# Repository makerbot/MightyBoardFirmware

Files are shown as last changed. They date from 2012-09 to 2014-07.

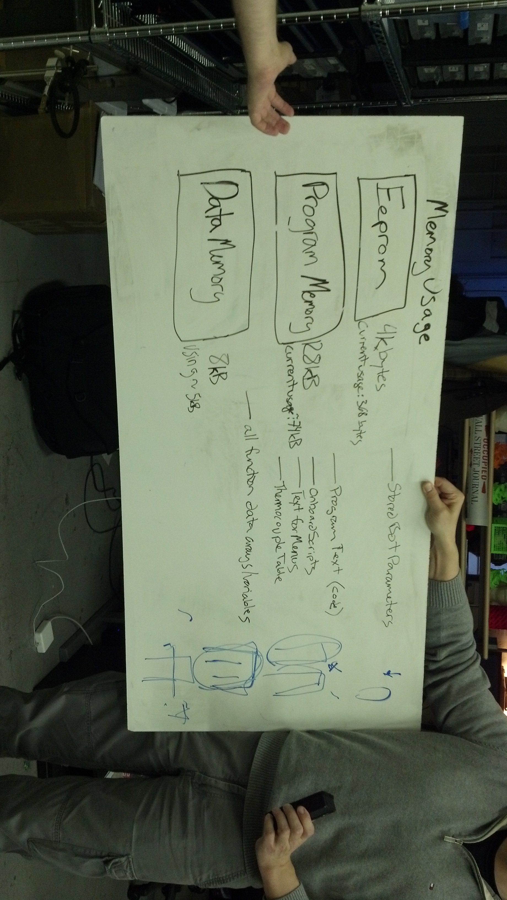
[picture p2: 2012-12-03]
docs/memory_usage.jpg

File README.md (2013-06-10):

Replicator MightyBoard Firmware
===============================

This is the firmware repository for the Replicator, Replicator Dual, Replicator 2 & 2X desktop 3D-printing machines.

If you're getting started, please begin by reading the documentation for
the firmware:
http://wiki.makerbot.com/v2-firmware

This project contains the following subdirectories:
* firmware - this is the firmware, where active development takes place.
       See http://wiki.makerbot.com/v2-firmware for details on how to
       build and install the code.
* bootloader - this contains the bootloaders for the MCUs on the Mightyboard
* dist - this directory contains tools and scripts for quickly installing
       bootloaders and board images for the MightyBoard
* tests - this directory contains tests using the s3g driver and development testing data
* docs - info about command handling and firmware details

N.B. to generate the french version of the firmware, add the LOCALE=fr env
variable before compiling

To use the tests in s3g_tests, you must initialize the s3g submodule by running
git submodule init
git submodule update

Build the latest firmware version
===

___These instructions only apply to Mac OS X for now.___

You must first install `SCons` and `avr-libc` if you don't have it :

    $ brew install scons

Then :

    $ brew tap larsimmisch/avr
    $ brew install avr-libc --env=std

If you wish to upload, you must install `avrdude` if it is not yet present :

    $ brew install avrdude

> NB : if you haven't got `brew` installed, see http://mxcl.github.io/homebrew/ .

Make sure that you have installed the command line tools from Xcode. If you run into any problem while compiling, it may mean that you need to update your developer folder :

    $ sudo xcode-select -switch /Applications/Xcode.app/Contents/Developer/

If everything is fine, you should be able to run `xcrun -find gcc` and have the following output :

    $ xcrun -find gcc
    /Applications/Xcode.app/Contents/Developer/usr/bin/gcc

And at least these packages :

    $ brew list 
    [...] avr-binutils  avrdude  avr-gcc   avr-libc  libmpc  mpfr  scons [...]

To create the documentation, you will also need `doxygen` (and `graphviz` for nice vizualisations) :

    $ brew install doxygen
    $ brew install graphviz

Then, run :

    $ ./firmware/build_and_upload.sh

You will be prompted for the Replicator type (A or B for `mighty_one` or `mighty_two`, default: `mighty_two`) and the locale to use (available : `fr` and `en`, default : `en`). The script will build the firmware from the sources in the given locale and ask to upload to the connected Replicator.

> NB : A build output log is generated in `./firmware/build_and_upload.log`

Cleaning up
===

You can clean up a previously built version with :

    $ ./firmware/cleanup.sh [-f]

The `-f` option cleans up without prompting for confirmation.

Uploading only
===

To upload a new firmware to a Replicator via USB :

    $ ./dist/MightyBoard/load_firmware_usb.sh mighty_two_v7.3.10.hex /dev/tty.usbmodem*

where `mighty_two_v7.3.10.hex` is the corresponding firmware HEX file and `/dev/tty.usbmodem*` the port to use (this is the default port for all USB connectors on a Mac).

- - -
 
Credits 
=======

  - French localization ( < 7.2 ) : guyzmo (CKAB)
  - French localization ( > 7.2 ) : tchapi (CKAB)
  - Scripts improvements, updates and fixes : tchapi (CKAB) - 2013

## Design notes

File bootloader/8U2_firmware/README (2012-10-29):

The Makerbot usbserial 8U2 firmware is based on Arduino's 8U2 usbserial firmware.  Thanks Arduino! (www.arduino.cc)
...And that firmware is based on LUFA (See the LUFA/readme.txt and LUFA/License.txt file).

The Makerbot 8U2 Source Code can be found in the src/Projects/makerbot directory

*Note, a .inf Driver file is required to use the MightyBoard with windows.  It can be found in the ReplicatorG drivers folder.

TO DOWNLOAD THE HEX FILE:
1. Connect the AVR ISP MKII compatible programmer to the 8U2 6 pin programming header
2. Ensure the Board is Powered
3. navigate to the directory containing the .hex file in the terminal
4. Execute the following avrdude command: avrdude -p at90usb82 -F -P usb -c avrispmkii -U flash:w:Makerbot-usbserial.hex -U lfuse:w:0xFF:m -U hfuse:w:0xD9:m -U efuse:w:0xF4:m -U lock:w:0x0F:m
5. If unsuccessful ("Error in USB Receive"), try again.  It sometimes takes a few tries

IF YOU NEED TO RECOMPILE THE HEX FILE:
*This is only necessary if you have made changes to the 8U2 Source Code
*This works with avr-gcc v4.3.3 on Mac osx.  It does not work with avr-gcc v4.5.3 on ubuntu. Testing with alternate gcc versions has not been done
1. Enter the makerbot project directory in the terminal
2. Run "make clean"
3. Run "make"
4. Your hex file will be generated in the currect directory

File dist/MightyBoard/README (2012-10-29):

#Uploading bootloaders + firmware

To use the firmware upload script, you must have avrdude installed on your machine.  To install, see instructions here: http://wiki.makerbot.com/v2-firmware

Note that these instructions include installing scons and avr-gcc which are tools required to build the firmware from source.  If you just want to upload firmware binaries using the scripts in this folder, you can skipp these steps and just install avrdude.

We use an avrisp mkii to upload bootloaders.  Other isp tools can be used, just edit the .sh script appropriately.  The avirisp mkii has a red line on the cable indicating pin one.  On the mighty_board one (revE), pin one is indicated with a small circle.  On Mightyboard two (revG), pin one is indicated with a longer white line next to the pin.

From the command line run:

./load_firmware.sh firmware_filename.hex usb_port

-firmware_filename.hex is the .hex binary firmware file  (default: mighty_two_v5.5.hex)
-usb_port is the port used to upload firmware over usb (default: /dev/ACM0)

1. wait for script prompt for 8U2
2. connect the avrisp mkii to the ISP pins for the 8U2, press enter
3. wait for script prompt for 1280 bootoader
4. connect the avrisp mkii to the ISP pins for the 1280, press enter
5. (occasional step) if the script asks you to switch a fuse back (y/n), choose y
6. wait for the script prompt for the 1280 firmware
7. connect the usb cable to the mightyboard usb port, remove the avisp mkii from the 1280 ISP pins, press enter

the script will report success or fail for each step.  if you have failures, the script runs in a loop and you can run it again by continuing to press enter.  if all steps are successful, hit control-C to quit

#Uploading firmware only via USB
(bootloaders must be loaded for upload over USB to work)

from the command line run:

./load_firmware_usb.sh firmware_filename.hex usb_port

-firmware_filename.hex is the .hex binary firmware file  (default: mighty_two_v5.5.hex)
-usb_port is the port used to upload firmware over usb (default: /dev/ACM0)

press enter when prompted to upload firmware.  keep in mind the following:

1. mightyboard must be connected to usb_port
2. mightyboard must be powered on
3. bootloaders must be loaded successfully prior
4. the serial port cannot be open with repG or other serial host
5. the auto reset will not work if the serial port has not been opened immediately prior with pyserial or avrdude @ 57600baud.  If this is the case, use pyserial or avrdude to open a connection to the board at 115200 (or any baud rate not 57600), then run ./load_firmware_usb.sh again and the auto reset will work.  alternatively, you can manually press the reset button on the mightyboard at the same moment as starting the script to force a reset.

if upload is successfull, press control-C to exit.  if desired, the script will run in a loop indefinitely.

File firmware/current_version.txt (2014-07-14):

7.6.1.1.0
 * PID loop values changed to handle Rep2X extruder heating issues
 * (PID loop) ErrorAccumulator max set to 512 instead of 256
7.5.5.1.0
 * Fix for change filament timeouts ending in non-resumable prints
7.5.4.1.0
 * Update to Rep1(Dual) statup script so that loading the right extruder makes sense
7.5.3.1.0
 * Fix for heat hold USB print canceling scenarios
7.5.2.1.0
 * Fix for heat hold interfering with preheat, and filament loading after a canceled build
7.5.1.1.0
 * Removal of dual filament loading for Rep2X startup script
 * Fix for Heat Hold not being handled properly
 * Fix for bot type errors causing builds to "unattach" from the UI
 * Fix for bot type errors causing builds to not return to the SD Menu
7.4.1.1.0
 * Fix for build time rollover bug, 
 * Added fix for the button array setup
 * Disable z pause when a build is canceled
7.3.13.1.0
 * fix box display bug in heat up
7.3.12.1.0
 * HBP update rate set to 500ms
7.3.11.1.0
 * fixed bug in heating up bar, updated z pause height behavior
7.3.210.1.0
 * testing version to check for memory overruns
7.3.10.1.0
 * Added feature to return the screen to the SD Card menu after an SD card build.
7.3.9.1.0
 * Fixed alignment issues in Menu_locales.hh
7.3.8.1.0
 * Fixed JIRA bug MW-946. When the printer is in the paused state and the user presses "Back to Monitor", the print resumes.
7.3.7.1.0
 * Fixed JIRA bug MW-952. Following a mid-print filament change, the "Resume Build" item is still available on the menu.
7.3.6.1.0
 * Fixed not resetting of Z Pause Height enable after a Z Pause Height condition.
 * Changed behaviour of Done! within Z Pause Height menu, it now goes to the build screen.
7.3.5.1.0
 * Fixed bug preventing user from resuming their print after a timeout in the change filament mode.
7.3.4.1.0
 * Changed behaviour of Z Pause Height behaviour, it now goes into active build menu when triggered
7.3.3.1.0
 * Added timeout to change filament mode as the motors are staying at full torque
 * Corrected issue that prevented the printer from checking for heaters not working
7.3.2.1.0
 * Fixed temperature conversion table inconsistencies
 * Added error numbers to all heater failures
 * Added new errors for heater failures that check for proper configuration byte to be read back from both channels
 * Some heater failures now cause the printer to stop printing
 * Added slower SD card fix for Rev H boards
7.3.1.1.0
 * XY motor torque is no longer turned down when in Change Filament mode allowing the print to resume from the same spot easier on Rep 2x
 * Added Z Pause Height feature, pausing the print at a specified height in mm
 * Fixed missing letters in text displayed on LCD
 * Added print time, toggle between percent complete and print time
 * Corrected some inconsistencies with temperature reading tables
7.2.1.1.0
 * removed post level print
7.1.3.1.0
 * fixed text alignment issue
7.0.0.1.0
 * french build - not going to worry about the fact the the french makerbots have a slightly different versioning scheme
7.1.3.1.0
 * fixed text alignment issue
7.1.2.1.0
 * fixed "retry" in level plate
 * fixed the LevelPlate TestPrint brokeness
7.1.1.1.0
 * beta version of 7.1 - the LevelPlate TestPrint is broken in this build
7.0.8.1.0
 * fixes issue in ReplicatorG where the bot starts before the extruder reaches temperature
7.0.7.1.0
 * fixes to preheat behavior and sleep
7.0.6.1.0
 * sd card menu reversed
7.0.5.1.0
 * heat behavior fixes, 2X support adds
7.0.3.1.0
 * version number bump since we haven't release in a while 
7.0.1.1.0
 * x3g version number bump
6.2.30.1.0
 * x3g firmware, active build menu re-org
6.2.29.1.0
 * tall boy firmware for aljosa
6.2.28.1.0
 * enable reversed for Ben and Harry 
6.2.27.1.0
 * edit eeprom map to fix downgrade breakage
6.2.26.1.0
 * minor version number bumped to 2 to accomodate a bug fix on 6.0
6.1.26.1.0
 * internal release only minor updates required for future
6.1.25.1.0
 * internal release middle updates
6.1.24.1.0
 * internal release with stream version numbers
6.1.23.1.0
 * internal release with stream version numbers
6.1.22
 * internal release with jetty acceleration + eeprom changes
6.0.21
 * this is a merge of the jetty acceleration (more better!)
6.0.20
 * same as 5.05.20 with major version number bumped to 6.0
5.05.20
 * internal release - release candidate September 16 2012
5.05.19
 * internal release September 13 2012
6.00.18
 * internal release September 12 2012
5.05.16
 * internal release August 31, interface minor re-org
5.05.15
 * internal release August 23, minor menu fixes
5.05.14
 * internal release August 23, small bug fixes
5.05.13
 * internal release August 21, interface final beta
5.05.12
 * internal release August 17, 2012 with nozzle offsets updated
5.05.09
 * internal release August 13, 2012 no z-clipping version for engineering.
5.06.08
 * internal release Sept 12, 2102
5.05.07
 * internal release July 31, 2012 interface feature updates
5.05.06
 * internal release July 26, 2012 build for mighty_one
5.05.04
 * internal release July 18, 2012 debug stalls using atomic blocks on move commands
5.05.03
 * internal release July 18, 2012, pause menu updates
5.05.02
 * internal release July 12, 2012, replicactor 2 steps per mm
5.05.01
 * internal release July 12, 2012
5.05
 * release for acceleration
5.04
 * fixes for acceleration
5.03
 * bug fix release / acceleration beta
5.02
 * added Tolerance offset for nozzles

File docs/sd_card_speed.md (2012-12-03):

##SD Card Speed Requirements

Note: We should measure both the command processing time and the sd card block read time with the logic analyzer to have a more accurate estimate.  

SD Card Block: 512 Bytes (we read sd card data in blocks at a time)

Command Buffer: 512 Bytes

Extended Move Command: 31 bytes

Moves per Block : 16 moves (512/31)

Approximate time for command processing : 2ms (we should measure this again - this estimate is from memory)

Time to Process 1 block of commands : 32ms (16 *2ms -- subject to check above)

Note: Timing was measured at unknown start/ end points - timing may not be multiplicative, ie only a portion of the time between start,end may be doubling.  So to get accurate times, we may need to measure again.  

Time to read one Block @ 8MHz : 2.5ms

estimated times to read one block at sd card clock speeds :

4MHz    5ms

2MHz    10ms

1MHz    20ms

500kHz  40ms (at this point we are slower than the Time to process 1 block of commands)

Time to send one command with serial interface: 4ms

Time to send 16 commands with serial interface: 64ms

Thus at 250kHz, we are slower than serial transfer (subject to re-measuring the processing and block read times)

Print time tests were done using the nut and bolt print (circular + small features) at 8MHz, 1MHz and 500kHz clock speeds with no appreciable print time difference

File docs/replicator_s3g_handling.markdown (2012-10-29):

# Replicator Handling of s3g commands

## Overview

This document describes the way that the Replicator firmware handles s3g commands. Specifically what payload values are accepted, and how unaccepted values are handled.   We only list commands that have behaviors different than those described in the general s3g specification @  https://github.com/makerbot/s3g/blob/master/doc/s3g_protocol.markdown

## Packet Errors
Currently, the Replicator does not return error codes for invalid packets, instead the packet process times out.  If the packet has an invalid CRC, invalid length, etc.  The packet will not be processed and the s3g host will timeout waiting for a response.  
The Replicator does return special response codes in the following cases (these are not related to packet communication errors)

* Build_Cancel : user has canceled an active host build
* Active_Build : bot is  building from SD card, or running an onboard script, no action commands can be processed
* CMD_Unsupported : bot does not understand the received command

## Ignored Commands (return "success", but take no action)

### Host Query Commands
* 01 Initialize to Boot State

There is no "Command not supported/recognized" packet response for Tool and Host Action commands.  This is because action commands are placed in a queue and are not processed immediately. The bot returns a "Success"  code for Action commands as long as the buffer has space, and the bot is not printing from SD card.  The following action commands are ignored by the replicator:

### Host Action Commands
* 133 - Delay

### Tool Action Commands

*01 - init: reset firmware
*06 - Set motor speed  
*10 - Enable / disable motor
*14 - Set servo 1 position
*24 - Abort

## Unhandled Query Commands (return "cmd unknown")

### Host Query Commands
*26 Get Communication Stats

### Tool Query Commands
*17 Get Motor Speed
*25 Read from EEPROM
*26 Write to EEPROM

## Commands With Limited or specialized behavior

### Host Query Commands

#### 00 - Get version: Query firmware for version information
    HostVersion < 25 : returns firmware version 0x0000 (ie invalid version)
    HostVersion > 25 : returns motherboard firmware version

#### 03 - Clear buffer: Empty the command buffer
    a soft reset is called.  same as abort, and reset

#### 10 - Tool query: Query a tool for information
    There is no separate "tool", but the replicator upholds this format.  Tool query commands with respond with the expected behaviors (except as noted in the tool section of this doc).  For example, get toolhead temperature responds with the tool temperature, even though the tool is not technically separate from the motherboard

#### 12 - Read from EEPROM
    we use the avr eeprom library for eeprom access.  This may or may not handle invalid values for offset and length
    TODO: hanldle invalid values for offset and length.   Currently the bot attemts to process all values.

#### 13 - Write to EEPROM
    we use the avr eeprom library for eeprom access.  This may or may not handle invalid values for offset and length
    TODO: hanldle invalid values for offset and length.  Currently the bot attemts to process all values.

#### 22 - Extended stop: Stop a subset of systems
    a zero response is always sent.  There is no processed failure case

### Host Buffered Commands

#### 131 - Find axes minimums: Move specified axes in the negative direction until their limit switch is triggered.
    The Replicator does not have minimum endstops for X or Y.  Thus get axes minimum for these axes will result in steppers trying to move past the minimum point. (ie bad things will happen) 
    A and B axes also do not have minimum axes, and this command will simply timeout

#### 132 - Find axes maximums: Move specified axes in the positive direction until their limit switch is triggered.
    The Replicator does not have maximum endstops for Z.  Thus get axes maximum for the Z axes will result in the stepper trying to move past the maximum point. (ie bad things will happen) 
    A and B axes also do not have minimum axes, and this command will simply timeout
    
#### 135 - Wait for tool ready : Wait until a tool is ready before proceeding
    Tool ID is expected to be 0 or 1.  Other values will assume tool 0.
    nominal timeout values are not implemented, all values accepted for timeout. 
    The delay parameter is ignored
    A tool timeout of zero will not wait for the tool to heat.  

#### 136 - Tool action command: Send an action command to a tool for execution
    There is no separate "tool", however tool commands will return the expected values (with the exceptions noted in the "tool" section).  For example, set tool temperature will set the extruder temperature, even though the extruder is controlled locally at the motherboard.

#### 137 - Enable/disable axes: Explicitly enable or disable stepper motor controllers
  The current version of the accelerated firmware ignores this command while printing.  The stepper system enables axes when they are moved and disables them on reset

#### 139 - Queue extended point
Z clipping is implemented.  If a z_axis position greater than 150 is queued, the replicator will clip movement to 150

#### 140 - Set extended position
Z clipping is implemented.  If a z_axis position greater than 150 is queued, the replicator will clip movement to 150

#### 141 - Wait for platform ready: Wait until a build platform is ready before proceeding
    the bot has no knowledge of nominal values.
    Tool ID is ignored.
    Delay is ignored
    Timeout accepts all values.  A timeout of 0 or small will not wait for the tool to heat

#### 142 - Queue extended point, new style
Z clipping is implemented.  If a z_axis position greater than 150 is queued, the replicator will clip movement to 150

#### 145 - Set digital potentiometer value
    max value is 118.  This is due to the wide tolerance of the resistors on the Mightyboard, which make voltage levels variable. values above 118 will be clipped

#### 146 - Set RGB LED value
    Replicator cannot provide full RGB coverage.  It has two PWM output channels and ON/OFF options.  Thus two LEDs can be set to a full range of brightness levels and the third one must be on/off

#### 147 - Set Beep
    There are occasional timing issues with the handling of this command that result in mangled or missed buzzes.
    frequencies above 4978 are equivalent to full on.

#### 151 - Queue Song
    songIDs > 2 are set to song ID 2

### Tool Query Commands

#### 00 - Get version: Query firmware for version information
    motherboard firmware version is returned

#### 25 - Read from EEPROM
    reads from motherboard eeprom.  note that the eeprom maps are not the same between 5.x and previous firmware versions.

#### 26 - Write to EEPROM
    writes to  motherboard eeprom.  note that the eeprom maps are not the same between 5.x and previous firmware versions.

# Tool Action Commands

#### 03 - Set toolhead target temperature
    values less than 0 will be set to zero
    values greater than max temp (currently 280) will be set to max temp

#### 31 - Set build platform target temperature
    values less than 0 will be set to zero
    values greater than max temp (currently 280) will be set to max temp

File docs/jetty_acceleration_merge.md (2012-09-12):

### Issues ###
Set digipot s3g not working (likely from bug in Buttons)

### Make sure to check ###
jetty does not disable the stepper interrupt on command:pause() - is this behavior replicated elsewhere?
are the nozzle offsets still implemented properly?
lets run a test with the new offsets
can we print from USB?  from repG?  from Makerware? - is the slow down flag different for RepG / Makerware
verify that the pipelining behavior still works and enable disable axes are not getting in the way
test sleep and pause commands for correct position recall
the eeprom map + update all the headers for the eeprom map

### issues with build! ###
jog mode not working correctly
steppers not being disabled at end of print
sleep does not work anymore......no sleep, does pause, text is weird
isEnabled menu item is not working

### first build checks  -- all checked ###
steps per mm definitions
sqrt table - no definitions for this anywhere else
check if we are using axis_lengths anywere - I store 1/2 lengths for xy and jetty stores full...
are we writing to build_Status_bytes?

stopBuild vs stopBuildNow (a new add) - this is present in the jetty firmware  - It looks like this just facilitates the cancel plate down behavior... so not to worry

### fixes that need to be ported to the "stable" build ###
cancel build menu fix
sd card name fix

### things that are probably good that we should merge in step 2 ###
move things out of Motherboard.cc in favor of ? being defined in the class that is using them?
moving screen definitions out of Motherboard.cc if they are duplicates of other definitions
? are .h file function definitions worse for some reason?  a memory reason?
filament tracker
jetty mods to jog mode
track down all the warnings - ignore some warnings
move TOTAL_BUILD_TIME back to 0x01A0 in the eepromMap

### Merge Progess ###
computing the distance etc values:
in firmware: 0.35 - 0.7 ms
on host: 0.2 - 0.4 ms
comparable points : 0.2ms vs 0.4 ms

##File Name Changes##
MBI files Planner.xx, Steppers.xx (movements called from Command.xx, Host.xx, Menu.xx)
Jetty files StepperAccelPlaner.xx, StepperAccel.xx, StepperAxis.xx, Steppers.xx, StepperAccelSpeedTable* (movments called from same)

StepperAccelPlannner.xx->Planner.xx
StepperAccel.xx->Steppers.xx
Steppers.xx top level namespace : calls StepperAccel functions, performs initialization functions
StepperAxis.xx define ports, initialize stepper axes, define read write functions to steppers
StepperAccelSpeedTable (a lookup table for stepper rates)

Advance
two constants are stored in eeprom: K, K2

StepperAxis.hh
  update e_steps in dda_step if JKN_ADVANCE is defined
Configuration.hh
  defines JKN_ADVANCE
StepperAccelPlanner.hh
  if JKN_ADVANCE is defined, the block struct contains extra fields: use_advance_lead, advance_lead_entry, advance_lead_exit, advance_pressure_relax, advance_lead_prime, advance_lead_deprime

All behavior only occurs if JKN_ADVNACE is defined:
StepperAccel.cc
  define advance_state, advance_pressure_relax_accumulator, lastAdvanceDeprime, ADVANCE_INTERRUPT_FREQUENCY = 10000, st_extruder_interrupt_rate, extruder_interrupt_steps_per_call, st_extruder_interrupt_rate_counter
  if current_block->use_accel and deprime_enabled, for each extruder, if extruder is stepping in this block and it has been deprimed, if extruden_when_negative, subtract extruder_deprim_stpes from e_steps, if ADVANCE_LEAD_DE_PRIME, also subtract block_avance_lead_prime from e_steps, else add these values to e_steps , set deprimed to false (extrude_when_negative indicates the direction we tell the steppers to move in order to push plastic)
  if current_block has no extruder steps, apply deprime, which the same logic as for applying prime, with the direction reversed (ie subtract steps to deprime, add steps to prime
  if use_accel, for each extruder, if avance_state==ACCEL, shift_phase16(advance_lead_entry), if advace_state==DECEL, shift_phase16(-advance_lead_exit), shift_phase32(-advance_pressure_relax_accumulator >> 8)
  call stepperAcisSetHardwareEnabledToMatch only when e_steps[x] are 0
  if decel leg is starting, update advance_state and advance_pressure_relax_accumulator
  if all steps completed, update lastAdvanceDeprime[]
  extruder interrupt is defined (where extruder steps are taken)
  compute the number of steps we take per extruder interrupt (there is a separate interrupt for the extruders with a fixed frequency of 10kHz)
  in block setup, set advance_state to ACCEL
StepperPlannerAccel.cc
  define extruder_advance_k, extruder_advance_k2 and initialize them
  final_speed_step_rate function defined : this is a fixed point function to compute the final speed of the block.  not sure why it is only defined with JKN_ADVANCE, 
  in calculate_trapezoid:
    clear the advance variables
    if advance_lead true for the block, compute final step rate
    if JKN_ADVANCE_LEAD_ACCEL : advance_lead_entry = extruder_advance_k * accelration rate, else advance_lead_entry = extruder_advance_k * (max_rate - initial_rate)
    advance_lead_prime = extruder_advance_k * initial_rate - KCONSTANT_0_5 (used when there is no previous e move, ie extruder starts from 0)
    advance_lead_entry and advance_lead_prime are capped to be greater or equal 0 (neagtive indicates overflow)
    advance_lead_exit and advance_lead_deprime are computed in exactly the same way.
    advance_pressure_relax = extruder_advance_k2 * acceleration_rate * KCONSTANT_100 / decelerate_steps
    advance_pressure_relax, advance_lead_exit and adance lead_deprime are capped to be greater or equal to 0 (negative indicates overflow)
    store these values in the current block_t
  in planner_add, block->use_advance_lead is true when there is a non-zero stepper move and the advance constants are not set to zero
Motherboard.cc
  calls doExtruderInterrupt() from within timer2 interrupt, which also manages the micros timer and the blinking leds

advance_pressure_relax_accumulator
  accumulates current_block->advance_pressure_relax each step of the deceleration phase, and this is applied as a shift_phase32 in the advance section of the stepper interrupt

lastAdvanceDeprime
  set by calculations of previous block, applied in the negative direction when the buffer is empty, or the extruder steps are zero

shift_phase functions
adding steps to the counter for the axis, slowing down or speeding up when the stepps occur for this axis

Deprime
Can only be enabled if ADVANCE is enabled
deprime is forced on if advance is enabled (it is forced on in steppers::reset())
deprime adds steps to esteps, which are exectuted whenever the extruder interrupt executes - these are extra steps in addition to the steps specified in the G1 command
deprime steps look to be on the order of 10s, up to 1xx  - so this is roughly equivalent to a retract of 1mm

Jerk
jerk applied to all axes, scaling factor applied to current speed as well as vmax_junction.  this means that the jerk for the next segment will be computed using the vmax_junction speed instead of the nominal speed.....

Homing System

Buffer System for planner blocks

Command States and calling move functions

Acceleration On vs Acceleration Off

New move Commands describe

What is a good plan for getting the TOM to work with the new tool chain?
a) implement the new command
b) modify the firmware to accept old style commands (cost?)

movement calls within Host and Menu.cc

fixed point vs float

stepper timer
timer 3.  

dda_step vs regular?  
there is no regular.  dda is the name of the struct containing the relevant stepper info like counter, delta etc

SRAM_tests

OVERSAMPLED_DDA

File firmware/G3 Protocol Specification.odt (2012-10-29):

G3 Protocol (FW v 4.02 & newer)

Overview

Where to find implementations of this protocol

Firmware

Host software

Network Overview

Packet Protocol

Protocol Overview

Timeouts

Handling Packet Failures

Command Buffering

Packet structure

Command structure

Host Commands

Slave Commands

Slave IDs

Response Packets

Response Packet Payload Structure

Test Commands

0x70 - Echo test

0x71 - Generate bad response packet

0x72 - Simulate bad packet reception

0x73 - Passthru to slave

0x74 - Clear command queue

0x75 - "NO SUCH COMMAND" command

0x76 - Set Debug Code

0x77 - Get Debug Code

0x78 - Get Debug Buffer

0xF0 - Command queue filler

Master Microcontroller Commands (3-axis controller)

Query Commands

0 - Get Version - Query firmware for version information

1 - Init - Initialize firmware to boot state

2 - Get Available Buffer Size - Determine how much free memory we have for buffering.

3 - Clear Buffer - Empty the command buffer

4 - Get Position - Get the current position of the tool

6 - Set Range - Set the maximum range of travel on all axes. - OBSOLETE

7 - Abort Immediately - Stop Machine, Shut Down Job Permanently

8 - Pause / Unpause - Halt Execution Temporarily

9 - Probe - Move in Z axis (negative) until probe hits something

10 - Tool Query - Query a tool for information

11 - Is Finished - See if the machine is currently doing anything

12 - Read from EEPROM

13 - Write to EEPROM

14 - Capture to file

15 - End capture

16 - Playback capture

17 - Reset

18 - Get next filename

19 - Read debug registers

20 - Get firmware build name

21 - Get Extended Position - Get the current position on 5 axes

22 - Extended Stop - Stop subset of systems

23 - Get Motherboard Status

24 - Build Start Notification

25 - Build End Notification

26 - Get communication statistics

Buffered Commands

128 - RESERVED (Obsolete command)

129 - Queue point

130 - Set Position

131 - Find Axes Minimums - Blocking seek to hardware min switches, w/ timeout

132 - Find Axes Maximums - Blocking seek to hardware max switches w/ timeout

133 - Delay - Simply stop and wait.

134 - Change Tool - Switch to a new tool

135 - Wait For Tool Ready - Wait until a tool is ready before proceeding

136 - Tool Action Command - Send an action command to a tool for execution

137 - Enable/Disable Axes - Explicitly power or depower steppers

138 - User Block

139 - Queue extended point

140 - Set Extended Position

141 - Wait For Platform Ready - Wait until the build platform is ready before proceeding

142 - Queue extended point, new style

143 - Store Home Positions

144 - Recall Home Positions

Slave Microcontroller Commands (Extruder)

Query Commands

0 - Get Version

1 - Init - Initialize firmware to boot state

2 - Get Temperature

3 - Set Target Temperature

4 - Set Motor 1 Speed (PWM)

5 - Set Motor 2 Speed (PWM)

6 - Set Motor 1 Speed (RPM)

7 - Set Motor 2 Speed (RPM)

8 - Set Motor 1 Direction

9 - Set Motor 2 Direction

10 - Toggle Motor 1 (on/off)

11 - Toggle Motor 2 (on/off)

12 - Toggle Fan (on/off)

13 - Toggle Valve (on/off)

14 - Set Servo 1 Position

15 - Set Servo 2 Position

16 - Filament Status

17 - Get Motor 1 Speed (RPM)

18 - Get Motor 2 Speed (RPM)

19 - Get Motor 1 Speed (PWM)

20 - Get Motor 2 Speed (PWM)

21 - Select Tool

22 - Is Tool Ready?

23 - Pause/Unpause - Halt Execution Temporarily

24 - Abort - Terminate all operations and reset

25 - Read from EEPROM

26 - Write to EEPROM

30 - Get Build Platform Temperature

31 - Set Build Platform Target Temperature

32 - Get Extruder Target Temperature

33 - Get Build Platform Target Temperature

34 - Get firmware build name

35 - Is Build Platform Ready?

36 - Get Tool Status

37 - Get PID state

38 - Set Motor 1 Speed (DDA)

39 - Set Motor 2 Speed (DDA)

40 - Light indicator LED

Changes and additions to the protocol

Errata

# Overview

This document describes the protocol by which 3rd and 4th generation RepRap electronics communicate with their host machine, as well as the protocol by which the RepRap host communicates with its subsystems. The same simple packet protocol is used for both purposes.

# Where to find implementations of this protocol

# Firmware

The default firmware for the default generation 3 electronics can be found on GitHub at http (http://github.com/makerbot/G3Firmware):// (http://github.com/makerbot/G3Firmware)github (http://github.com/makerbot/G3Firmware). (http://github.com/makerbot/G3Firmware)com (http://github.com/makerbot/G3Firmware)/ (http://github.com/makerbot/G3Firmware)makerbot (http://github.com/makerbot/G3Firmware)/ (http://github.com/makerbot/G3Firmware)G (http://github.com/makerbot/G3Firmware)3 (http://github.com/makerbot/G3Firmware)Firmware (http://github.com/makerbot/G3Firmware).

# Host software

Currently the only software suite implementing this protocol is ReplicatorG. It can be found on GitHub at http (http://github.com/makerbot/ReplicatorG):// (http://github.com/makerbot/ReplicatorG)github (http://github.com/makerbot/ReplicatorG). (http://github.com/makerbot/ReplicatorG)com (http://github.com/makerbot/ReplicatorG)/ (http://github.com/makerbot/ReplicatorG)makerbot (http://github.com/makerbot/ReplicatorG)/ (http://github.com/makerbot/ReplicatorG)ReplicatorG (http://github.com/makerbot/ReplicatorG).

# Network Overview

The RepRap Generation 3 electronics set consists of several hardware components:

1. A single Master Controller which controls the 3-axis steppers, communicates with a host PC, supports a storage card and controls a set of toolheads.
2. A set of Stepper Drivers which drive the steppers based on signals from the master controller. The communications between the drivers and the master controller is outside of the scope of this document.
3. A number of Tool Controllers which control extruders, cutters, frostruders, etc.

The two communications channels covered by this document are:

1. The Host Network, between a host computer and the master controller
2. The Slave Network, between the master controller and one or more tool controllers.

The host network is generally implemented over a standard TTL-level RS232 serial ion. The slave network is implemented as an RS485 serial bus driven by SN75176A transceivers.

# Packet Protocol

# Protocol Overview

Each network has a single master: in the case of the host network, this is the host computer, and in the case of the slave network, this is the master controller. All network communications are initiated by the network master; a slave node can never initiate a data transfer.

Data is sent over the network as a series of simple packets. Packets are variable-length, with a maximum payload size of 32 bytes.

Each network transaction consists of at least two packets: a master packet, followed by a response packet. Every packet from a master must be responded to.

Commands will be sent in packets. All commands are query/response. The master in each pair will always initiate communications, never the slave. All packets are synchronous; they will wait for a response from the client before sending the next packet. The firmware will continue rendering buffered commands while receiving new commands and replying to them.

# Timeouts

Packets must be responded to promptly. No command should ever block. If a query would require more than the timeout period to respond to, it must be recast as a poll-driven operation.

All communications, both host-mb and mb-toolboard, are at 38400bps. It should take approximately 1/3rd ms. to transmit one byte at those speeds. The maximum packet size of 32+3 bytes should take no more than 12ms to transmit. We establish a 20ms. window from the reception of a start byte until packet completion. If a packet is not completed within this window, it is considered to have timed out.

It is expected that there will be a lag between the completion of a command packet and the beginning of a response packet. This may include a round-trip request to a toolhead, for example. This window is expected to be 36ms. at the most. Again, if the first byte of the response packet is not received by the time 36ms. has passed, the packet is presumed to have timed out.

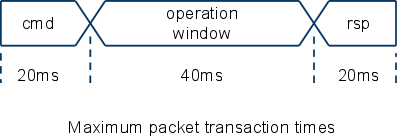
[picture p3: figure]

# Handling Packet Failures

If a packet has timed out, the host or board should treat the entire packet transaction as void. It should:

- Return its packet reception state machine to a ready state.
- Presume that no action has been taken on the transaction
- Attempt to resend the packet, if it was a host packet.

# Command Buffering

To ensure smooth motion, as well as to support print queueing, we'll want certain commands to be queued in a buffer. This means we won't get immediate feedback from any queued command. To this end we will break commands down into two categories: action commands that are put in the command buffer, and query commands that require an immediate response. In order to make it simple to differentiate the commands on the firmware side, we will break them up into two sets: commands numbered 0-127 will be query commands, and commands numbered 128-255 will be action commands to be put into the buffer. The firmware can then simply look at the highest bit to determine which type of packet it is.

Every packet gets precisely one response packet. Query commands must be sent in their own packet. Only action or query commands can be sent in a single packet. The first byte of the command payload will determine the nature of the entire packet. Thus, you cannot mix query and action commands in a single packet!

Command Types

Range | Type | Description
0-127 | Query Commands | Commands that can be executed immediately, and thus do not need to be queued. Generally return pre-calculated information and should be fast.
128-255 | Action Commands | Commands that must be executed one at a time, and in a particular order. These commands should be buffered for smooth operation. Many of there commands may take up a large amount of time to complete.

# Packet structure

Command packets are sent from the Master to the Slave. This can either be from the Host CPU to the Master uC or from the Master uC to the Slave uC. It consists of a two-byte header, a variable-length payload, and a 1 byte CRC footer.

The packet consists of:

Index | Name | Details
0 | Start byte | This byte always has the value 0xD5 and is used to ensure synchronization.
1 | Length | This byte indicates the length of the payload (excluding the header and CRC) in bytes.
2... | Payload | The packet payload. This is appended to the buffer and either immediately executed and removed (if a query type) or buffered for execution (if an action type).
Length+2 | CRC | This is the 8-bit iButton/Maxim CRC of the payload.

Command length is implicit in the command structure; no explicit separator is needed.

# Command structure

# Host Commands

The payload of a packet consists of one command. Each command contains a header, as follows:

Index | Name | Details
0 | Command | The command code to send to the device.
1-N | Arguments | Arguments to this command (details below as 'command payload').

# Slave Commands

The payload of a packet consists of one command. Each command contains a header, as follows:

Index | Name | Details
0 | Slave ID | The ID of the slave device being addressed. The value 127 represents any available device; see below. New as of firmware version 2.92. Previously, 255.
1 | Command | The command code to send to the device.
2-N | Arguments | Arguments to this command (details below as 'command payload').

# Slave IDs

The slave ID is the ID number of a toolhead. A toolhead may only respond to commands that are directed at its ID. If the packet is corrupt, the slave should *not* respond with an error message to avoid collisions.

The exception to this is the slave ID 127. This represents any listening device. The address 127 should only be used when setting the ID of a slave.

New as of firmware version 2.92. Previously, the broadcast address was 255.

# Response Packets

Response packets look just like command packets. The only difference is the payload is guaranteed to contain a response code as the first byte, as described below. The only exception is certain debugging packets, which will specifically indicate such in their description.

# Response Packet Payload Structure

Index | Name | Details
0 | Response Code | This is a standard response code that is included with all packets and is described below.
1-N | Response Data | This contains response-specific data. Length is implicit based on the command being responded-to.

If the command was a non-request command, the response data is always empty.

Response Code Values

Note: These are changed starting in version 2.92. Previously, they were 0x0 - 0x7.

Response Code | Interpretation
0x80 | Generic error, packet discarded.
0x81 | Success.
0x82 | Action buffer overflow, entire packet discarded.
0x83 | CRC mismatch, packet discarded.
0x84 | Query packet too big, packet discarded.
0x85 | Command not supported/recognized.
0x86 | Success; expect more packets. Used when a single reponse packet cannot contain the entire message to be retrieved.
0x87 | Downstream timeout (for example, a toolhead timed out).

Data Formats

The protocol is a byte-oriented protocol. Payloads may contain various information in a variety of formats, but will generally be limited to the formats described below. Multi-byte datatypes will always be transmitted in Little-endian mode. Remember, this means that the least significant byte ("littlest") byte is sent first! For a more in-depth discussionof little-endian storage, see: http (http://en.wikipedia.org/wiki/Endianness#Little-endian):// (http://en.wikipedia.org/wiki/Endianness#Little-endian)en (http://en.wikipedia.org/wiki/Endianness#Little-endian). (http://en.wikipedia.org/wiki/Endianness#Little-endian)wikipedia (http://en.wikipedia.org/wiki/Endianness#Little-endian). (http://en.wikipedia.org/wiki/Endianness#Little-endian)org (http://en.wikipedia.org/wiki/Endianness#Little-endian)/ (http://en.wikipedia.org/wiki/Endianness#Little-endian)wiki (http://en.wikipedia.org/wiki/Endianness#Little-endian)/ (http://en.wikipedia.org/wiki/Endianness#Little-endian)Endianness (http://en.wikipedia.org/wiki/Endianness#Little-endian)# (http://en.wikipedia.org/wiki/Endianness#Little-endian)Little (http://en.wikipedia.org/wiki/Endianness#Little-endian)- (http://en.wikipedia.org/wiki/Endianness#Little-endian)endian (http://en.wikipedia.org/wiki/Endianness#Little-endian)

Various Data Types

Type | Range
uint8 | 0 to 255
uint16 | 0 to 65,535
int16 | -32767 to 32,767
uint32 | 0 to 4,294,967,295
int32 | -2,147,483,647 to 2,147,483,647

# Test Commands

The command codes of the form 0xFX and 0x7X are reserved for diagnostic test packets. The firmware is not guaranteed to implement any of these operations.

# 0x70 - Echo test

This command indicates that the client should resend the original packet data, minus the echo test byte. The client will not send a response code-- the remaining payload will be copied verbatim. This will persuade the client to send any valid packet the host wants.

Payload: variable.

Response: resend of payload.

# 0x71 - Generate bad response packet

This command will request that the client respond with a test packet that exhibits the given error.

1 | No response
2 | Skip start byte
3 | Bad packet length (specified length too long)
4 | Bad/incorrect CRC
5 | Start byte, then timeout

Payload: 1 byte.

uint8: Error type to simulate.

# 0x72 - Simulate bad packet reception

This command will essentially instruct the recipient to behave as if the received packet had experienced the specified error. The error codes are:

1 | Received noise
2 | Bad packet length (specified length too long)
3 | Bad/incorrect CRC
4 | Timeout

Payload: 1 byte.

uint8: Error type to simulate.

# 0x73 - Passthru to slave

This command will pass the enclosed packet on to its slave bus, and return a copy of the returned packet if the packet receipt is successful. If the packet receipt is unsuccessful (for example, if the packet times out) it should return a generic error. The client will not send a response code if successful-- instead it will just mirror as much of the packet as possible.

Payload: N bytes.

The payload of the packet to send to the slave bus.

Response: N bytes.

Complete payload of response packet, truncated to fit if necessary.

# 0x74 - Clear command queue

This command will clear the command queue completely and immediately.

Payload: 0 bytes.

# 0x75 - "NO SUCH COMMAND" command

This command code has no definition, and is reserved an an unimplemented command for test purposes.

# 0x76 - Set Debug Code

This command sets the blink code for the target board. Setting the code to '0' will turn off the debug code.

Payload: 2 bytes.

uint8: the debug register to set. Should always be '0'.

uint8: the value to set the debug register to. For register '0', the number of blinks to display.

Response: 0 bytes.

# 0x77 - Get Debug Code

Retrieve the value of a debug register. '0' is the debug register containing the blink code. Other registers are undefined.

Payload: 1 byte.

uint8: the debug register to read. Should always be '0'.

Response: 1 byte.

uint8: the value of the debug register.

# 0x78 - Get Debug Buffer

(only on the firmware_debug branch in github/makerbot:G3Firmware)

Retrieve the contents of the debug buffer and clears it.

Response: N bytes.

The current contents of the debug buffer, the data in the buffer is whatever the firmware puts in there.

# 0xF0 - Command queue filler

This is a nop command that will remain on the command queue until cleared. It may specify padding bytes to help fill space on the buffer.

Payload: 1 + N byte.

uint8: the number of padding bytes following this byte. The total space on the command buffer will be 2+N.

uint8 * N: padding bytes. The actual values are ignored.

# Master Microcontroller Commands (3-axis controller)

# Query Commands

# 0 - Get Version - Query firmware for version information

This command allows the host and firmware to exchange version numbers. It also allows for simple automated discovery of the firmware. Version numbers will always be stored as a single number, Arduino / Processing style. Thus, the versions will be 0 to 65535.

Payload (2 bytes) - host version

uint16: Host Version.

Response (2 bytes) - firmware version

uint16: Firmware Version

# 1 - Init - Initialize firmware to boot state

Initialization consists of:

  - resetting current position to 0,0,0
  - clearing command buffer
  - setting range to eeprom value (if it exists) otherwise its 0.

Payload (0 bytes)

Response (0 bytes)

# 2 - Get Available Buffer Size - Determine how much free memory we have for buffering.

This command will let us know how much buffer space we have available for action commands. It can be used to determine if and when the buffer is available for writing. If we are writing to the SD card, it will generally always report the maximum number of bytes available.

Payload (0 bytes)

Response (4 bytes)

uint32: number of bytes available in the command buffer.

# 3 - Clear Buffer - Empty the command buffer

This command will empty our buffer, and reset all pointers, etc to the beginning of the buffer. If writing to an SD card, it will reset the file pointer back to the beginning of the currently open file. Obviously, it should halt all execution of action commands as well.

Payload (0 bytes)

Response (0 bytes)

# 4 - Get Position - Get the current position of the tool

Useful for determining current position of the toolhead. It is up to the host software to add or subtract the toolhead offset to determine the actual position of the toolhead. It will also return the status of the various endstops for diagnostic information.

Payload (0 bytes)

Response (13 bytes)

int32: current x position, in steps

int32: current y position, in steps

int32: current z position, in steps

uint8: bits marked for endstop status: (7-0) : | N/A | N/A | z max | z min | y max | y min | x max | x min |

~~5 -~~ ~~Get~~ ~~Range~~ ~~-~~ ~~Get~~ ~~the~~ ~~maximum~~ ~~range~~ ~~of~~ ~~travel~~ ~~on~~ ~~all~~ ~~axes~~~~. -~~ ~~OBSOLETE~~

~~When~~ ~~find~~ ~~axes~~ ~~maximums~~ ~~is~~ ~~called~~~~,~~ ~~it~~ ~~will~~ ~~record~~ ~~the~~ ~~maximum~~ ~~as~~ ~~the~~ ~~range~~~~.~~ ~~internally~~~~,~~ ~~it~~ ~~will~~ ~~keep~~ ~~track~~ ~~of~~ ~~its~~ ~~range~~ ~~and~~ ~~this~~ ~~function~~ ~~will~~ ~~simply~~ ~~report~~ ~~that~~ ~~internal~~ ~~value~~~~.~~ ~~We~~ ~~cannot~~ ~~assume~~ ~~that~~ ~~there~~ ~~are~~ ~~endstop~~ ~~switches~~ ~~for~~ ~~all~~ ~~axes~~ ~~at~~ ~~b~~~~oth~~ ~~min~~ ~~and~~ ~~max~~ ~~positions~~~~.~~ ~~The~~ ~~firmware~~ ~~will~~ ~~know~~ ~~this~~~~,~~ ~~so~~ ~~the~~ ~~"~~~~Find~~ ~~Axes~~ ~~min~~~~/~~~~max~~~~"~~ ~~commands~~ ~~may~~ ~~be~~ ~~partially~~ ~~no~~~~-~~~~ops~~ ~~in~~ ~~this~~ ~~case~~~~.~~ ~~The~~ ~~firmware~~ ~~should~~ ~~always~~ ~~respect~~ ~~this~~ ~~range~~ ~~and~~ ~~never~~ ~~go~~ ~~beyond~~ ~~it~~~~.~~

~~Payload~~ ~~(0~~ ~~bytes~~~~)~~

~~Response~~ ~~(12~~ ~~bytes~~~~)~~

~~uint~~~~32~~~~:~~ ~~x~~ ~~range~~~~,~~ ~~units~~ ~~in~~ ~~steps~~

~~uint~~~~32~~~~:~~ ~~y~~ ~~range~~~~,~~ ~~units~~ ~~in~~ ~~steps~~

~~uint~~~~32~~~~:~~ ~~z~~ ~~range~~~~,~~ ~~units~~ ~~in~~ ~~steps~~

# ~~6~~ ~~-~~ ~~Set~~ ~~Range~~ ~~-~~ ~~Set~~ ~~the~~ ~~maximum~~ ~~range~~ ~~of~~ ~~travel~~ ~~on~~ ~~all~~ ~~axes~~~~. -~~ ~~OBSOLETE~~

~~This~~ ~~command~~ ~~tells~~ ~~the~~ ~~firmware~~ ~~what~~ ~~its~~ ~~maximum~~ ~~range~~ ~~of~~ ~~travel~~ ~~is~~~~.~~ ~~The~~ ~~firmware~~ ~~should~~ ~~always~~ ~~respect~~ ~~this~~~~.~~ ~~This~~ ~~should~~ ~~be~~ ~~recorded~~ ~~into~~ ~~the~~ ~~eeprom~~ ~~for~~ ~~future~~ ~~usage~~~~.~~

~~Payload~~ ~~(12~~ ~~bytes~~~~)~~

~~uint~~~~32~~~~:~~ ~~x~~ ~~range~~~~,~~ ~~units~~ ~~in~~ ~~steps~~

~~uint~~~~32~~~~:~~ ~~y~~ ~~range~~~~,~~ ~~units~~ ~~in~~ ~~steps~~

~~uint~~~~32~~~~:~~ ~~z~~ ~~range~~~~,~~ ~~units~~ ~~in~~ ~~steps~~

~~Response~~ ~~(0~~ ~~bytes~~~~)~~

# 7 - Abort Immediately - Stop Machine, Shut Down Job Permanently

This function is intended to be used to terminate a print during printing. Extruder and accessories off, steppers disabled, everything shuts down.

Payload (0 bytes)

Response (0 bytes)

# 8 - Pause / Unpause - Halt Execution Temporarily

This function is intended to be called infrequently by the end-user in order to make build-time adjustments immediately and easily. No buffers or other run-time variables are changed. The pause command should also prompt the firmware to send a pause command to the toolhead.

On pause, it stops all movement, stops extrusion, moves up a 'safe z' amount, and waits for new commands.

On unpause, it lowers to original Z, optionally restarts extrusion, and resumes movement.

agm: Currently we do not do the "safe Z" backoff. I'd like to introduce that as a parameter instead.

Payload (0 bytes)

Response (0 bytes)

# ~~9~~ ~~-~~ ~~Probe~~ ~~-~~ ~~Move~~ ~~in~~ ~~Z~~ ~~axis~~ ~~(~~~~negative~~~~)~~ ~~until~~ ~~probe~~ ~~hits~~ ~~something~~

~~This~~ ~~command~~ ~~will~~ ~~wait~~ ~~until~~ ~~the~~ ~~buffer~~ ~~is~~ ~~clear~~ ~~to~~ ~~avoid~~ ~~conflicts~~~~.~~ ~~It~~ ~~will~~ ~~also~~ ~~prevent~~ ~~any~~ ~~buffered~~ ~~commands~~ ~~from~~ ~~executing~~ ~~for~~ ~~the~~ ~~duration~~ ~~of~~ ~~the~~ ~~probe~~~~.~~

~~Payload~~ ~~(6~~ ~~bytes~~~~)~~

~~uint~~~~32~~~~:~~ ~~feedrate~~ ~~(~~~~in~~ ~~microseconds~~ ~~between~~ ~~steps~~~~) (~~~~max~~ ~~71.58~~ ~~minutes~~~~)~~

~~uint~~~~16~~~~:~~ ~~timeout~~ ~~(~~~~in~~ ~~seconds~~ ~~before~~ ~~abort~~~~) (~~~~max~~ ~~= 18~~ ~~hours~~~~) (~~~~default~~ ~~= 1~~ ~~minute~~~~)~~

~~Response~~ ~~(4~~ ~~bytes~~~~)~~

~~uint~~~~32~~~~:~~ ~~Z~~ ~~position~~ ~~when~~ ~~probe~~ ~~has~~ ~~been~~ ~~triggered~~~~.~~

# 10 - Tool Query - Query a tool for information

This command is for sending a query to the tool. The master firmware will then pass the query along to the appropriate tool, as well as passing the response back as well. This allows the tool specific commands to be developed independently between.

Payload (2 + N bytes)

uint8: the index of the tool to query

uint8: the query command for the tool.

N bytes: command specific payload, variable size.

Response (0-N bytes)

0-N bytes: the command specific response, if any.

# 11 - Is Finished - See if the machine is currently doing anything

This command lets us know if the machine is finished executing its current command queue.

Payload (0 bytes)

Response (1 byte)

uint8: 0 if still in progress; 1 if finished.

# 12 - Read from EEPROM

Read the specified number of bytes from the given offset in the EEPROM and return it in the response packet. The maximum read size is 32 bytes.

Payload (3 bytes)

uint16: the offset of the read

uint8: the number of bytes to return, N. N <= 16.

Response (N bytes)

N bytes: the data read from the EEPROM.

# 13 - Write to EEPROM

Write the given bytes to the EEPROM starting at the specified location. The maximum payload size is 16 bytes.

Payload (3+N bytes)

uint16: the offset of the write

uint8: the length of the data

N bytes: the data to write

Response (1 byte)

uint8: the number of bytes successfully written.

# 14 - Capture to file

Capture all subsequent commands up to the next "end capture" command to a file with the given name on the SD card. The file will be stored in the root of the fat16 filesystem on the SD card. The maximum file name length permitted is 12 characters, including the '.' and file name extension. Welcome to the brave new world of MS-DOS 2.0!

Payload (N bytes)

N bytes: the name of the file in ascii, terminated with a null

Response (1 byte)

uint8: response code

- 0 if operation was successful
- 1 if no SD card was present
- 2 if SD card init failed
- 3 if partition table could not be read
- 4 if filesystem could not be opened
- 5 if root directory could not be opened
- 6 if SD card is locked

# 15 - End capture

Complete an ongoing file capture.

Payload (0 bytes)

Response (4 bytes)

uint32: the total size of the capture in bytes

# 16 - Playback capture

Play back a file containing captured data to the makerbot. The maximum file name length permitted is 12 characters, including the '.' and file name extension. While the makerbot is in playback mode, it will only respond to pause, unpause, and stop commands.

Payload (N bytes)

N bytes: the name of the file in ascii, terminated with a null

Response (1 byte)

uint8: response code

- 0 if playback successfully initiated
- 1 if no SD card was present
- 2 if SD card init failed
- 3 if partition table could not be read
- 4 if filesystem could not be opened
- 5 if root directory could not be opened
- 7 if file was not found

# 17 - Reset

Reset the board remotely. Useful for reprogramming the board without having to fiddle with switches. The board will reset immediately after sending the response.

Payload (0 bytes)

Response (0 bytes)

# 18 - Get next filename

Retrieve the next valid filename from the SD card. If a non-zero value is passed to the "restart" parameter, the file list will begin again from the start of the directory. The file list state will be reset if any other SD operations are performed.

Payload (1 byte)

uint8: restart (0 to continue reading, 1 to begin anew)

Response (N+1 bytes)

uint8: an SD response code, one of the following:

- 0 if operation was successful
- 1 if no SD card was present
- 2 if SD card init failed
- 3 if partition table could not be read
- 4 if filesystem could not be opened
- 5 if root directory could not be opened

N bytes: the name of the file in ascii, terminated with a null. If the operation was unsuccessful, this will be the empty string. Even if there was an SD card error, the null string should be returned.

# ~~19~~ ~~-~~ ~~Read~~ ~~debug~~ ~~registers~~

~~Retrieve~~ ~~the~~ ~~value~~ ~~in~~ ~~the~~ ~~specified~~ ~~debugging~~ ~~register~~~~.~~ ~~These~~ ~~are~~ ~~essentially~~ ~~"~~~~scratch~~~~"~~ ~~registers~~ ~~for~~ ~~development~~~~.~~ ~~All~~ ~~registers~~ ~~are~~ ~~8-~~~~bit~~~~.~~

~~0:~~ ~~number~~ ~~of~~ ~~CRC~~ ~~errors~~ ~~in~~ ~~extruder~~ ~~responses~~

~~1:~~ ~~number~~ ~~of~~ ~~malformed~~ ~~packet~~ ~~responses~~ ~~from~~ ~~extruder~~

~~2:~~ ~~number~~ ~~of~~ ~~timeouts~~ ~~on~~ ~~packet~~ ~~responses~~ ~~from~~ ~~extruder~~

~~Payload~~ ~~(1~~ ~~byte~~~~)~~

~~uint~~~~8:~~ ~~index~~ ~~of~~ ~~debug~~ ~~register~~

~~Response~~ ~~(1~~ ~~byte~~~~)~~

~~uint~~~~8:~~ ~~value~~ ~~of~~ ~~register~~

# 20 - Get firmware build name

New in version 2.3

Retrieve the firmware build name, which is a human-readable string describing the build. Names should be chosen with an eye towards disambiguating builds targeted for different tools.

Payload length limitations restrict this field to 31 characters.

Payload (0 bytes)

Response (N+1)

char[N+1]: a null-terminated string representing the build name

# 21 - Get Extended Position - Get the current position on 5 axes

New in version 2.4

Retrieve the current position of all axes that this machine supports.

Payload (0 bytes)

Response (22 bytes)

int32[n]: position of axis n, in steps.

int16: bits marked for endstop status: (A-0) : | b max | b min | a max | a min | z max | z min | y max | y min | x max | x min |

# 22 - Extended Stop - Stop subset of systems

New in version 2.7

Stop the stepper motor motion or other subsystems.

Payload (1 byte)

uint8: bitfield indicating which subsystems to shut down

bit 0: halt all stepper motion immediately.

bit 1: clear command queue.

Response (1 byte)

int8: Result code.

- 0 if command terminated normally and subsystems were stopped.
- 1 for generic error (command failed).

# 23 - Get Motherboard Status

Proposed for version 2.9

Retrieve some information about the motherboard

Payload (0 bytes)

Response (1 byte)

uint8: As below:

Bit | 7 | 6 | 5 | 4 | 3 | 2 | 1 | 0
Name | POWER_ERROR | N/A | WDRF | BORF | EXTRF | PORF | N/A | N/A

POWER_ERROR - An error was detected with the system power. For Gen4 electronics, this means ATX_5V is not present.

WDRF - Watchdog reset flag was set at restart

BORF - Brown out reset flag was set at restart

EXTRF - External reset flag was set at restart

PORF - Power-on reset flag was set at restart

# 23 - Build Start Notification

Implemented in 4.02, mighty board only

Tells the motherboard that it is about to begin a build, and provides some information about the job for status reporting. The maximum file name length permitted is 12 characters, including the '.' and file name extension.

Payload (4+N bytes)

uint32: Set number of steps in the build
N bytes: Length of name string (bytes)

# 24 - Build End Notification

Implemented in 4.02, mighty board only
Tells the motherboard that the current build has ended.

Payload (1 bytes)
uint8: Reason for build end (uint8 cause. 0 is normal ending, 1 is user cancel, 0xFF is cancel due to error or safety cutoff)

# 25 - Get communication statistics

Proposed for version 2.9

Gather statistics about toolhead communication.

Payload (5 bytes)

uint32: Number of packets received from the USB interface

uint32: Number of packets sent over the RS485 interface

uint32: Number of packets sent over the RS485 interface that were not responded to

uint32: Number of packet retries attempted

uint32: Number of bytes received over the RS485 interface that were discarded as noise

# Buffered Commands

# ~~128~~ ~~-~~ ~~RESERVED~~ ~~(~~~~Obsolete~~ ~~command~~~~)~~

# 129 - Queue point

This queues an absolute point to move to. This may make it easier to implement the host software, but it is much larger than the incremental points which will reduce your available command buffer size.

Payload (16 bytes)

int32: x coordinate (units are steps)

int32: y coordinate (units are steps)

int32: z coordinate (units are steps)

uint32: dda speed (in microseconds between steps on the max delta)

# 130 - Set Position

This command defines the current position of the toolhead as the given position. Ordinarily this is used to set a "home" position.

Payload (12 bytes)

int32: x position, in steps

int32: y position, in steps

int32: z position, in steps

# 131 - Find Axes Minimums - Blocking seek to hardware min switches, w/ timeout

This function will find the hardware minimum. It will home all axes at the same time, so it is up to the host software to generate two separate homing commands if you want to home the Z axis separately.

Payload (7 bytes)

uint8: axes flags, where bits 4-0 represent which axes to home: | N/A | N/A | N/A | B | A | Z | Y | X |

uint32: feedrate (in microseconds between steps) (max 71.58 minutes)

uint16: timeout (in seconds before abort) (max = 18 hours) (default = 5 minutes)

# 132 - Find Axes Maximums - Blocking seek to hardware max switches w/ timeout

This function will find the hardware maximum, or position overflow (2^32), whichever is first.

It should also record this to the eeprom for future use. This function fill move all axes simulataneously, so it is important to generate two separate commands if you want to seek the Z axis separately.

Payload (7 bytes)

uint8: axes flags, where bits 4-0 represent which axes to home: | N/A | N/A | N/A | B | A | Z | Y | X |

uint32: feedrate (in microseconds between steps) (max 71.58 minutes)

uint16: timeout (in seconds before abort) (max = 18 hours) (default = ??)

# 133 - Delay - Simply stop and wait.

Exactly what it says.

Payload (4 bytes)

uint32: delay period (in microseconds) (max 71.58 minutes)

# 134 - Change Tool - Switch to a new tool

This will trigger a tool change. If the firmware supports automated tool changing, it will initiate its tool-changing routine. If it doesn't, it simply updates its currently selected tool and moves on.

Payload (1 byte)

uint8: index/address of the desired tool to select

# 135 - Wait For Tool Ready - Wait until a tool is ready before proceeding

This command is used to tell the machine to wait (for example for the extruder to heat up, etc.) It will poll the device with the 'are you ready' command until it responds affirmative

Payload (5 bytes)

uint8: the index of the tool to wait for before printing.

uint16: the delay between query packets sent to the tool head in milliseconds (default: 100 milliseconds)

uint16: the timeout before continuing without tool ready in seconds (default: 1 minute)

# 136 - Tool Action Command - Send an action command to a tool for execution

This command is for sending an action to the command. The master firmware will then pass the query along to the appropriate tool, as well as passing the response back as well.

Payload (3 + N bytes)

uint8: the index of the tool to query

uint8: the command for the tool.

uint8: the length of the command payload (N)

N bytes: command specific payload, variable size.

# 137 - Enable/Disable Axes - Explicitly power or depower steppers

This command is used to explicitly power steppers on or off. Generally, it is used to shut down the steppers after a build to save power and avoid generating excessive heat.

Payload (1 byte)

uint8: bitfield

bit 7: 1 to enable, 0 to disable

bit 6,5: ignored

bit 4: Axis 4 (B axis) on

bit 3: Axis 3 (A axis) on

bit 2: Axis 2 (Z axis) on

bit 1: Axis 1 (Y axis) on

bit 0: Axis 0 (X axis) on

# 138 - User Block

This command will halt further processing of the command queue until the block is cleared by user intervention. The "Proceed" command will release the block. This is not equivalent to a pause-- if you want to perform any toolhead operations, like stopping extrusion, you need to do so in a seperate command prior.

Payload (2 bytes):

uint16: Block identifier.

# 139 - Queue extended point

This queues an absolute point to move to. This may make it easier to implement the host software, but it is much larger than the incremental points which will reduce your available command buffer size. This is the 5D equivalent of 129 - Queue Point.

Payload (24 bytes)

int32: x coordinate (units are steps)

int32: y coordinate (units are steps)

int32: z coordinate (units are steps)

int32: a coordinate (units are steps)

int32: b coordinate (units are steps)

uint32: dda speed (in microseconds between steps on the max delta)

# 140 - Set Extended Position

This command defines the current position of the toolhead as the given position. Ordinarily this is used to set a "home" position. This is the 5D equivalent of 130 - Set Position.

Payload (12 bytes)

int32: x position, in steps

int32: y position, in steps

int32: z position, in steps

int32: a position, in steps

int32: b position, in steps

# 141 - Wait For Platform Ready - Wait until the build platform is ready before proceeding

New in version 2.4

This command is used to tell the machine to wait until the build platform is ready (target temperature has been reached). It will poll the device with the 'are you ready' command until it responds affirmative.

Payload (5 bytes)

uint8: the index of the tool to which the build platform is attached

uint16: the delay between query packets sent to the tool head in milliseconds (default: 100 milliseconds)

uint16: the timeout before continuing without tool ready in seconds (default: 1 minute)

# 142 - Queue extended point, new style

New in version 2.7

This queues a point to move to. It differs from old-style point queues (see command 139 et. al.) in that it no longer uses the DDA abstraction and instead specifies the total move time in microseconds. Additionally, each axis can be specified as relative or absolute. If the "relative" bit is set on an axis, then the motion is considered to be relative; otherwise, it is absolute.

Payload (25 bytes)

int32: x coordinate (units are steps)

int32: y coordinate (units are steps)

int32: z coordinate (units are steps)

int32: a coordinate (units are steps)

int32: b coordinate (units are steps)

uint32: duration of movement in microseconds

uint8: relative or absolute motion

bit 7,6,5: ignored

bit 4: Axis 4 (B axis) relative

bit 3: Axis 3 (A axis) relative

bit 2: Axis 2 (Z axis) relative

bit 1: Axis 1 (Y axis) relative

bit 0: Axis 0 (X axis) relative

# 143 - Store Home Positions

New in version 2.8

Record the current axes positions to EEPROM.

Payload (1 byte)

uint8: As below:

Bit | 7 | 6 | 5 | 4 | 3 | 2 | 1 | 0
Name | N/A | N/A | N/A | B | A | Z | Y | X

# 144 - Recall Home Positions

New in version 2.8

Recall the axes positions stored in EEPROM.

Payload (1 byte)

uint8: As below:

Bit | 7 | 6 | 5 | 4 | 3 | 2 | 1 | 0
Name | N/A | N/A | N/A | B | A | Z | Y | X

145 – Set Digital Stepper Potentiometer Value

New in version 3.2; Mighty Board only

This command will set the value of the digital pototentiometer associated with a stepper motor. The digital potentiometer sets the reference voltage input for the stepper driver. Lower values will result in less current available to the motor. The potentiometers can set VREF from 0-1.7V.

Payload (2 bytes)

uint8: the stepper identifier. This value should be in the rang 0-4. 0 is X, 1 is Y, 2 is Z, 3 is A, 4 is B.

uint8: The value to set the digital potentiometer to. This value should be in the range 0-127. 0 is the lowest value; 127 the highest.

146 – Set RGB LED values

New in version 3.2; Mighty Board only

This command will set the brightness of the RGB LEDs in the bot.

Payload (3 bytes)

uint8: the R value. 0 turns the R channel off; 255 turns it fully on.

uint8: the G value. 0 turns the G channel off; 255 turns it fully on.

uint8: the B value. 0 turns the B channel off; 255 turns it fully on.

147 – Beep

New in version 3.2; Mighty Board only

This command will emit a beep from the piezo speaker.

Payload (4 bytes)

uint16: the frequency of the beep in Hz.

uint16: the length of the beep in ms.

148 – Pause for Button

New in version 4.02; Mighty Board only

This command will pause the bot for user interaction, ie pressing a button. When a button is pressed the commands continue.

Payload (4 bytes)

uint8: Mask of which buttons to accept. As of V 4.02 0xFF (any) is the only valid value

uint16: seconds to wait for interaction.

uint8: 1 for 'reset on timeout, 0 for 'do not reset on timeout'.

149 – Display Message

New in version 4.02; Mighty Board only

This command will display a message to the bot's onboard user interface, for informational or interface values. Often used with 148 to send info to the bot to get user interaction. NOTE: for word-wrapping of long , line wrap order is 0,2,1,3. Don't ask, it's complicated.

Payload (4 bytes min)

uint8: Options, must be 0 for ver 4.02

uint8: Starting X coordinate for display.

uint8: Starting Y coordinate for display.

uint8: display timeout in seconds. After timeout display returns to previous state/information.

uint8: (up to 25) string of characters to display, null terminated.

150 – Set Build Percentage

New in version 4.03; Mighty Board only

This command will manually override the the build complete % on the bot, overriding the existing build complete %. This will override build % for SD card events, and/or from the bot.

Payload (2 bytes)

uint8: the new build % in the range 0 – 100.

uint8: Reserved byte for future use

151 – Queue onboard song

New in version 4.03; Mighty Board only

This command will flag the bot to play a built-in song. Default songs are Error Sound (0), a Ta-da sound (1), and a warning sound (2). All other sounds are user or machine specific, with the warning song (2) the default for unknown sounds.

Payload (2 bytes)

uint8: The song ID to play.

uint8: Reserved byte for future use

152 – Reset to factory settings

New in version 4.03; Mighty Board only

This command will reset the motherboard to factory settings.

Payload (1 bytes)

uint8: reserved for future use. 0xFF expected.

# Slave Microcontroller Commands (Extruder)

# Query Commands

# 0 - Get Version

This command allows the master and slave to exchange version numbers. It also allows for simple automated discovery of the firmware. Version numbers will always be stored as a single number, Arduino / Processing style. Thus, the versions will be 0 to 65535.

Payload (2 bytes) - host version

uint16: Host Version

Response (2 bytes) - firmware version

uint16: Firmware Version

# 1 - Init - Initialize firmware to boot state

Initialization consists of:

  - setting desired temperature to zero
  - turning off all devices (fan, coolant, etc.)
  - detaching all servo devices
  - setting desired RPM / PWM to zero

Payload (0 bytes)

Response (0 bytes)

# 2 - Get Temperature

This returns the last recorded temperature. It's important for speed purposes that it does not actually trigger a temperature reading, but rather returns the last reading. The slave firmware should be constantly monitoring its temperature and keeping track of the latest readings.

Payload (0 bytes)

Response (2 bytes)

int16: Current Temperature in Celsius

# 3 - Set Target Temperature

This sets the desired temperature for the heating element. The slave firmware will then attempt to maintain this temperature as closely as possible.

Payload (2 bytes)

int16: Desired Target Temperature in Celsius

# 4 - Set Motor 1 Speed (PWM)

This sets the motor speed as a PWM value. Motor 1 generally corresponds to the extruder motor (M101-M103, M108 GCodes). It should not actually enable the motor until the motor enable command is given.

Payload (1 byte)

uint8: Desired PWM speed

# 5 - Set Motor 2 Speed (PWM)

This sets the motor speed as a PWM value. Motor 2 generally corresponds to the spindle motor (??? GCodes). It should not actually enable the motor until the motor enable command is given.

Payload (1 byte)

uint8: Desired PWM speed

# 6 - Set Motor 1 Speed (RPM)

This sets the motor speed as an RPM value. Motor 1 generally corresponds to the spindle motor (M101-M103, M108 GCodes). It should not actually enable the motor until the motor enable command is given. For this command to actually work, a quadrature encoder, or tachometer must actually be attached to the motor.

Payload (4 bytes)

uint32: speed in microseconds between complete rotations.

# 7 - Set Motor 2 Speed (RPM)

This sets the motor speed as an RPM value. Motor 1 generally corresponds to the spindle motor (??? GCodes). It should not actually enable the motor until the motor enable command is given. For this command to actually work, a quadrature encoder, or tachometer must actually be attached to the motor.

Payload (4 bytes)

uint32: speed in microseconds between complete rotations.

# 8 - Set Motor 1 Direction

This sets the desired rotation direction of the motor. It does not turn the motor on or off.

Payload (1 byte)

uint8: 0 = reverse / counter clockwise, 1 = forward / clockwise

# 9 - Set Motor 2 Direction

This sets the desired rotation direction of the motor. It does not turn the motor on or off.

Payload (1 byte)

uint8: 0 = reverse / counter clockwise, 1 = forward / clockwise

# 10 - Toggle Motor 1 (on/off)

This turns the motor on or off. It is possible to also set the direction of the motor as well. This makes the command fairly efficient, since you can turn the motor on while setting the direction as well. When the motor is enabled, it will move at the previously specified speed (either RPM or PWM).

Payload (1 byte)

uint8: The bottom two bits of this command determine direction and enable status:

Bit | 7 | 6 | 5 | 4 | 3 | 2 | 1 | 0
Name | N/A | N/A | N/A | N/A | N/A | N/A | DIR | ENABLE

ENABLE - HIGH means motor is enabled, LOW means motor is disabled.

DIR - HIGH means motor rotates Clockwise, LOW means motor rotates Counter Clockwise

# 11 - Toggle Motor 2 (on/off)

This turns the motor on or off. It is possible to also set the direction of the motor as well. This makes the command fairly efficient, since you can turn the motor on while setting the direction as well. When the motor is enabled, it will move at the previously specified speed (either RPM or PWM).

Payload (1 byte)

uint8: The bottom two bits of this command determine direction and enable status:

Bit | 7 | 6 | 5 | 4 | 3 | 2 | 1 | 0
Name | N/A | N/A | N/A | N/A | N/A | N/A | DIR | ENABLE

ENABLE - HIGH means motor is enabled, LOW means motor is disabled.

DIR - HIGH means motor rotates Clockwise, LOW means motor rotates Counter Clockwise

# 12 - Toggle Fan (on/off)

This turns the fan, or the output connected to the fan output on or off.

Payload (1 byte)

uint8: The bottom bit of this command determine enable status:

Bit | 7 | 6 | 5 | 4 | 3 | 2 | 1 | 0
Name | N/A | N/A | N/A | N/A | N/A | N/A | N/A | ENABLE

ENABLE - HIGH means fan is enabled, LOW means fan is disabled.

# 13 - Toggle Valve (on/off)

This opens the valve, or the output connected to the valve output on or off.

Payload (1 byte)

uint8: The bottom bit of this command determine enable status:

Bit | 7 | 6 | 5 | 4 | 3 | 2 | 1 | 0
Name | N/A | N/A | N/A | N/A | N/A | N/A | N/A | ENABLE

ENABLE - HIGH means valve is enabled (open), LOW means valve is disabled (closed).

# 14 - Set Servo 1 Position

This is basically just a wrapper to the Arduino hardware Servo library on pins 9 & 10. It supports full servo angles, and can also do continuous rotation: http (http://arduino.cc/en/Reference/Servo):// (http://arduino.cc/en/Reference/Servo)arduino (http://arduino.cc/en/Reference/Servo). (http://arduino.cc/en/Reference/Servo)cc (http://arduino.cc/en/Reference/Servo)/ (http://arduino.cc/en/Reference/Servo)en (http://arduino.cc/en/Reference/Servo)/ (http://arduino.cc/en/Reference/Servo)Reference (http://arduino.cc/en/Reference/Servo)/ (http://arduino.cc/en/Reference/Servo)Servo (http://arduino.cc/en/Reference/Servo)

Payload (1 byte)

uint8: desired angle (from 0 to 180)

# 15 - Set Servo 2 Position

This is basically just a wrapper to the Arduino hardware Servo library on pins 9 & 10. It supports full servo angles, and can also do continuous rotation: http (http://arduino.cc/en/Reference/Servo):// (http://arduino.cc/en/Reference/Servo)arduino (http://arduino.cc/en/Reference/Servo). (http://arduino.cc/en/Reference/Servo)cc (http://arduino.cc/en/Reference/Servo)/ (http://arduino.cc/en/Reference/Servo)en (http://arduino.cc/en/Reference/Servo)/ (http://arduino.cc/en/Reference/Servo)Reference (http://arduino.cc/en/Reference/Servo)/ (http://arduino.cc/en/Reference/Servo)Servo (http://arduino.cc/en/Reference/Servo)

Payload (1 byte)

uint8: desired angle (from 0 to 180)

# 16 - Filament Status

Payload (0 bytes)

Response (1 byte)

uint8: status: 0 - empty, 255 = full, number between 0-255 represents percentage of filament remaining.

# 17 - Get Motor 1 Speed (RPM)

Payload (0 bytes)

Response

uint32: speed in microseconds between complete rotations.

# 18 - Get Motor 2 Speed (RPM)

Payload (0 bytes)

Response

uint32: speed in microseconds between complete rotations.

# 19 - Get Motor 1 Speed (PWM)

Payload (0 bytes)

Response (1 byte)

uint8: current PWM value for the motor.

# 20 - Get Motor 2 Speed (PWM)

Payload (0 bytes)

Response (1 byte)

uint8: current PWM value for the motor.

# 21 - Select Tool

Tell a tool that it has been selected as the default tool. The tool may or may not choose to do anything with that information.

Payload (0 bytes)

Response (0 bytes)

# 22 - Is Tool Ready?

Asks the tool if it is ready to be used. Examples of ready states might be: spindle up to speed, temperature at target, etc.

Payload (0 bytes)

Response (1 byte)

uint8: 0 for not ready, 1 for ready.

# 23 - Pause/Unpause - Halt Execution Temporarily

Behaves in a similar fashion to the pause/unpause functionality of the motherboard.

Payload (0 bytes)

Response (0 bytes)

# 24 - Abort - Terminate all operations and reset

Behaves in a similar fashion to the abort functionality of the motherboard.

Payload (0 bytes)

Response (0 bytes)

# 25 - Read from EEPROM

Read the specified number of bytes from the given offset in the EEPROM and return it in the response packet. The maximum read size is 32 bytes.

Payload (3 bytes)

uint16: the offset of the read

uint8: the number of bytes to return, N. N <= 16.

Response (N bytes)

N bytes: the data read from the EEPROM.

# 26 - Write to EEPROM

Write the given bytes to the EEPROM starting at the specified location. The maximum payload size is 16 bytes. WARNING: this operation can be potentially slow (about 3.3ms * N) and will block all other operations. It's not recommended to write to the EEPROM while a build is in progress.

Payload (3+N bytes)

uint16: the offset of the write

uint8: the length of the data

N bytes: the data to write

Response (1 byte)

uint8: the number of bytes successfully written.

# 30 - Get Build Platform Temperature

This returns the last recorded temperature of the build platform. It's does not actually trigger a temperature reading, but rather returns the last reading. The slave firmware should be regularly monitoring its temperature and keeping track of the latest readings.

Payload (0 bytes)

Response (2 bytes)

int16: Current build platform temperature, in Celsius.

# 31 - Set Build Platform Target Temperature

This sets the desired temperature for the build platform element. The slave firmware will then attempt to maintain this temperature as closely as possible.

Payload (2 bytes)

int16: Desired build platform temperature, in Celsius.

# 32 - Get Extruder Target Temperature

New in v2.3 firmware

This command retrieves the last temperature set for the extruder.

Payload (0 bytes)

Response (2 bytes)

int16: The last set extruder temperature, in Celsius.

# 33 - Get Build Platform Target Temperature

New in v2.3 firmware

This command retrieves the last temperature set for the build platform.

Payload (0 bytes)

Response (2 bytes)

int16: The last set build platform temperature, in Celsius.

# 34 - Get firmware build name

New in version 2.5

Retrieve the firmware build name, which is a human-readable string describing the build. Names should be chosen with an eye towards disambiguating builds targeted for different tools.

Payload length limitations restrict this field to 31 characters.

Payload (0 bytes)

Response (N+1)

char[N+1]: a null-terminated string representing the build name

# 35 - Is Build Platform Ready?

New in version 2.6

Asks the heated build platform if it is ready to be used, typically waits for temperature to be reached.

Payload (0 bytes)

Response (1 byte)

uint8: 0 for not ready, 1 for ready.

# 36 - Get Tool Status

New in version 2.7

Retrieve some information about the current tool

Payload (0 bytes)

Response (1 byte)

uint8: As below:

Bit | 7 | 6 | 5 | 4 | 3 | 2 | 1 | 0
Name | EXTRUDER_ERROR | PLATFORM_ERROR | WDRF | BORF | EXTRF | PORF | N/A | EXTRUDER_READY

EXTRUDER_ERROR - HIGH means an error was detected with the extruder heater (if the tool supports one), LOW means it is fine. The extruder heater will fail if an error is detected with the sensor (thermocouple) or if the temperature reading appears to be unreasonable.

PLATFORM_ERROR - HIGH means an error was detected with the platform heater (if the tool supports one), LOW means it is fine. The platform heater will fail if an error is detected with the sensor (thermocouple) or if the temperature reading appears to be unreasonable.

WDRF - Watchdog reset flag was set at restart

BORF - Brown out reset flag was set at restart

EXTRF - External reset flag was set at restart

PORF - Power-on reset flag was set at restart

EXTRUDER_READY - HIGH means extruder has reached target temperature, LOW means it has not.

# 37 - Get PID state

New in version 2.7

Retrieve the state variables of the PID controller. This is intended for tuning the PID constants.

Payload (0 bytes)

Response (12 bytes)

int16: Extruder heater error term

int16: Extruder heater delta term

int16: Extruder heater last output

int16: Platform heater error term

int16: Platform heater delta term

int16: Platform heater last output

# 38 - Set Motor 1 Speed (DDA)

Proposed for 2.8 (RG)

This sets the stepper motor speed as a DDA value, or microseconds between steps. It should not actually enable the motor until the motor enable command is given. For future implementation of 5D (vs 4D) two DDA codes are sent - the DDA to start with and the DDA to end with. The third uint32 is the number of steps to take. The direction to go is set by code 8 - Set Motor 1 Direction.

Payload (12 bytes)

uint32: speed in microseconds between steps (start of movement).

uint32: speed in microseconds between steps (end of movement).

uint32: total steps to take.

# 39 - Set Motor 2 Speed (DDA)

Proposed for 2.8 (RG)

This sets the stepper motor speed as a DDA value, or microseconds between steps. It should not actually enable the motor until the motor enable command is given. For future implementation of 5D (vs 4D) two DDA codes are sent - the DDA to start with and the DDA to end with. The third uint32 is the number of steps to take. The direction to go is set by code 9 - Set Motor 2 Direction.

Payload (12 bytes)

uint32: speed in microseconds between steps (start of movement).

uint32: speed in microseconds between steps (end of movement).

uint32: total steps to take.

# 40 - Light indicator LED

Proposed for 2.9

This command turns on an indicator light (for gen 4, the motor direction LED). This command is intended to serve as visual feedback to an operator that the electronics are communicating properly. Note that it should not be used during regular operation, because it interferes with h-bridge operation.

# Changes and additions to the protocol

2011-6-20 This section was quite out of date, and has been removed.

# Errata

Homing. There appears to be multiple approaches to homing. I'll explain ours. If you do the same or know about other common approaches, we should find a good solution (MK):

  - When starting a print, we first home to hardware switches. The firmware knows in which direction to home; it will home in the negative direction in X/Y and in positive direction in Z. Positive Z means at it's maximum height about the base plane. Homing is done with a fast feedrate until the optical switches hit. Then we'll reverse direction and move very slowly until the optical switches are clear again. This will give us a very accurate absolute reference position. ZH: Yes, this is exactly what the homing command will do.pushd

MK: We don't yet have a "homing command", only "find axes min/max". Idea: We could create a new command, "Goto Reference", which will home to the defined reference position (which may be a combination of min and max for the three axes). The find axes min/max would then only be needed to record the working area (range), and could then be joined into a separate command (Find Range). The range could of course be (partially) hardcoded into the firmware if the necessary switches are not present. Find Range would take a while to execute, but that's ok. We could even save the current range in EEPROM. ZH: I'd really like to keep the firmware as simple as possible, and move this type of complicated zero-point initialization into the host side of things. Really, all we're talking about here is something that could easily be represented as a series of commands (range: find min x/y/z, find max x/y/z, get range) or (goto reference: home xyz, goto X, Y, Z) additionally, the logic on these types of things is something that could change from machine to machine, and people will want to experiment with themselves. putting it on the host means we're much more flexible (ie: we could have a <reference> block of gcode that is user-editable for setting reference points.

MK: I'm still leaning towards putting more of this in firmware. The firmware still needs to be configured somehow (pin mapping, supported features, endstop positions, axis layoutt; which direction is positive vs. negative), and I think the reference configuration belongs together with this and not in run-time configuration sent from the host. We could make all this configurable over serial and store the configuration in EEPROM. It's a bit scary though (it's to easy to destroy hardware with software if someone presses the wrong button). I suggest that we investigate this by testing out different approaches in practice on our respective hardware setups by supporting multiple approaches in the initial phases and discuss this further later on.

agm: I really like the idea of storing the range in EEPROM. We could have a retrieve range that returns null if it has not been set yet, and a calibrate command that would find and store the range. (A subsequent retrieve would get the updated data.)

- Now, we'll move to the logical origin. This is configured on the host side since it needs to be calibrated every time we change the extruder head or exchange the printing base plate. In the future, this position would change for each model in a batch print. This will move the extruder head so that it touches the base plate (depending on local experience). In the future, this calibration could be automated by probing for the Z depth (e.g. using a piezo sensor embedded into the base plate, or a simple contact exploiting that the extruder head is conductive and grounding it). ZH: This can be accomplished by queuing an absolute point after it has homed to hardware switches. MK: Exactly.
- Set the current position to (0, 0, 0). This is what the g-code file expects; the local origin of the object currently being printed. For future batch printing, we should probably reset this for each object, after repeating ZH: This can/should also be accomplished by sending a 'set position' command after the previous two steps complete. MK: Yeps. agm: is there any reason for the hardware to know or care what the local zero is? Why not just have the driver feed it commands relative to the absolute limit-switch zero? MK: True enough. The logic for handling this will be on the host side, as well as any batching support. One thing we should think about though: How do we integrate this with the SD-card, LCD panel and autonomous printing ideas? Let's make this a separate section.
- From our machines.xml: ZH: This will work exactly as it has before... the joy of a driver-based system that understands gcode at a high level. MK: Perfect
- <warmup> M103 (extruder off) G90 (abs) G30 X0 Y0 Z0 F780 M104 S215.0 (heat) G0 X120.00 Y110.00 Z-104.50 F780 G92 (Metalab define current as home) </warmup> <cooldown> G91 (Metalab relative positioning) G1 Z10 F780 (move up) </cooldown>

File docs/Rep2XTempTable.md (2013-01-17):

# Temperature Table for recording Temperatures for the Rep2X's Thermistor
Because different thermistor tables have been used to ascertain these readings, they can only be used to find relative differences between thermocouple locations. 

## Table:
All temperature were taken with a Fluke Type k Thermocouple.  Temperatures were set with RepG, and given ~2 minutes to settle.  In the event of a constant oscillating temperature, the average was recorded.  Temperatures above 70°C tended to oscillate more than temperatures below.

<table>
<tr>
    <th>target</th>
    <th>MightyBoard</th>
    <th>Fluke Type K Thermocouple</th>
</tr>
<tr>
    <td>30°C</td>
    <td>30°C</td>
    <td>31.3°C</td>
</tr>
<tr>
    <td>40°C</td>
    <td>40°C</td>
    <td>39.8°C</td>
</tr>
<tr>
    <td>50°C</td>
    <td>49°C</td>
    <td>47.8°C</td>
</tr>
<tr>
    <td>60°C</td>
    <td>60°C</td>
    <td>56.6°C</td>
</tr>
<tr>
    <td>70°C</td>
    <td>70°C</td>
    <td>65.6°C</td>
</tr>
<tr>
    <td>80°C</td>
    <td>80°C</td>
    <td>74.0°C</td>
</tr>
<tr>
    <td>90°C</td>
    <td>90°C</td>
    <td>84.0°C</td>
</tr>
<tr>
    <td>100°C</td>
    <td>100°C</td>
    <td>92.3°C</td>
</tr>
<tr>
    <td>110°C</td>
    <td>110°C</td>
    <td>101.8°C</td>
</tr>
<tr>
    <td>120°C</td>
    <td>120°C</td>
    <td>109.6°C</td>
</tr>
<tr>
    <td>130°C</td>
    <td>130°C</td>
    <td>117.0°C</td>
</tr>
</table>

## Fine Grain testing

<table>
<tr>
    <th>target</th>
    <th>MightyBoard</th>
    <th>Fluke Type K Thermocouple</th>
</tr>
<tr>
    <td>30</td>
    <td>31</td>
    <td>32.0</td>
</tr>
<tr>
    <td>35</td>
    <td>36</td>
    <td>36.0</td>
</tr>
<tr>
    <td>40</td>
    <td>41</td>
    <td>40.5</td>
</tr>
<tr>
    <td>45</td>
    <td>45</td>
    <td>44.7</td>
</tr>
<tr>
    <td>50</td>
    <td>50</td>
    <td>48.5</td>
</tr>
<tr>
    <td>55</td>
    <td>55</td>
    <td>52.8</td>
</tr>
<tr>
    <td>60</td>
    <td>60</td>
    <td>57.6</td>
</tr>
<tr>
    <td>65</td>
    <td>65</td>
    <td>63.0</td>
</tr>
<tr>
    <td>70</td>
    <td>70</td>
    <td>68.0</td>
</tr>
<tr>
    <td>75</td>
    <td>75</td>
    <td>72.5</td>
</tr>
<tr>
    <td>80</td>
    <td>80</td>
    <td>77.0</td>
</tr>
<tr>
    <td>85</td>
    <td>85</td>
    <td>81.5</td>
</tr>
<tr>
    <td>90</td>
    <td>90</td>
    <td>86.15</td>
</tr>
<tr>
    <td>95</td>
    <td>95</td>
    <td>91.0</td>
</tr>
<tr>
    <td>100</td>
    <td>100</td>
    <td>95.15</td>
</tr>
<tr>
    <td>105</td>
    <td>105</td>
    <td>99.5</td>
</tr>
<tr>
    <td>110</td>
    <td>110</td>
    <td>104.5</td>
</tr>
<tr>
    <td>115</td>
    <td>115</td>
    <td>108.85</td>
</tr>
<tr>
    <td>120</td>
    <td>120</td>
    <td>113.15</td>
</tr>
<tr>
    <td>125</td>
    <td>125</td>
    <td>117.25</td>
</tr>
<tr>
    <td>130</td>
    <td>130</td>
    <td>121.5</td>
</tr>
<tr>
    <td>135</td>
    <td>135</td>
    <td>125.9</td>
</tr>
</table>

## With new Thermistor Table
<table>
<tr>
    <th>target</th>
    <th>MightyBoard</th>
    <th>Fluke Type K Thermocouple</th>
</tr>
<tr>
    <td>30</td>
    <td>31</td>
    <td>31</td>
</tr>
<tr>
    <td>35</td>
    <td>36</td>
    <td>35.6</td>
</tr>
<tr>
    <td>40</td>
    <td>41</td>
    <td>41.2</td>
</tr>
<tr>
    <td>45</td>
    <td>45</td>
    <td>45.8</td>
</tr>
<tr>
    <td>50</td>
    <td>50</td>
    <td>50.5</td>
</tr>
<tr>
    <td>55</td>
    <td>55</td>
    <td>56.0</td>
</tr>
<tr>
    <td>60</td>
    <td>60</td>
    <td>61.84</td>
</tr>
<tr>
    <td>65</td>
    <td>65</td>
    <td>66.85</td>
</tr>
<tr>
    <td>70</td>
    <td>69</td>
    <td>70.95</td>
</tr>
<tr>
    <td>75</td>
    <td>75</td>
    <td>75.45</td>
</tr>
<tr>
    <td>80</td>
    <td>80</td>
    <td>80.25</td>
</tr>
<tr>
    <td>85</td>
    <td>85</td>
    <td>84.9</td>
</tr>
<tr>
    <td>90</td>
    <td>90</td>
    <td>90.0</td>
</tr>
<tr>
    <td>95</td>
    <td>95</td>
    <td>94.85</td>
</tr>
<tr>
    <td>100</td>
    <td>100</td>
    <td>100</td>
</tr>
<tr>
    <td>105</td>
    <td>105</td>
    <td>105.7</td>
</tr>
<tr>
    <td>110</td>
    <td>110</td>
    <td>109.8</td>
</tr>
<tr>
    <td>115</td>
    <td>115</td>
    <td>114.8</td>
</tr>
<tr>
    <td>120</td>
    <td>120</td>
    <td>119.7</td>
</tr>
<tr>
    <td>125</td>
    <td>125</td>
    <td>124.9</td>
</tr>
<tr>
    <td>130</td>
    <td>130</td>
    <td>130</td>
</tr>
</table>

## Multiple Thermocouple Data
<table>
<tr>
    <th>Target Temp</th>
    <th>Next To Thermistor (Fluke)</th>
    <th>Middle of bed bottom (Chan 0)</th>
    <th>Middle of bed top (Chan 1)</th>
</tr>
<tr>
    <td>34</td>
    <td>34</td>
    <td>32.8</td>
    <td>32.2</td>
</tr>
<tr>
    <td>48</td>
    <td>47.8</td>
    <td>47.9</td>
    <td>45.6</td>
</tr>
<tr>
    <td>58</td>
    <td>58.2</td>
    <td>58.5</td>
    <td>54.7</td>
</tr
<tr>
    <td>66</td>
    <td>66.8</td>
    <td>67.4</td>
    <td>62.0</td>
</tr>    
<tr>
    <td>74</td>
    <td>74.6</td>
    <td>75.2</td>
    <td>68.7</td>
</tr>
<tr>
    <td>81</td>
    <td>81.6</td>
    <td>82.6</td>
    <td>74.8</td>
</tr>    
<tr>
    <td>88</td>
    <td>88.3</td>
    <td>89.5</td>
    <td>80.3</td>
</tr>    
<tr>
    <td>94</td>
    <td>94.8</td>
    <td>96.0</td>
    <td>85.7</td>
</tr>    
<tr>
    <td>104</td>
    <td>101.7</td>
    <td>103.2</td>
    <td>91.6</td>
</tr>    
<tr>
    <td>112</td>
    <td>108.4</td>
    <td>110.0</td>
    <td>97.0</td>
</tr>    
<tr>
    <td>119</td>
    <td>115.4</td>
    <td>117.2</td>
    <td>102.0</td>
</tr>    
<tr>
    <td>127</td>
    <td>122.8</td>
    <td>125.2</td>
    <td>108.7</td>
</tr>    
<tr>
    <td>135</td>
    <td>131.2</td>
    <td>134.3</td>
    <td>115.7</td>
</tr>
<tr>
    <td>157</td>
    <td>141.2</td>
    <td>144.3</td>
    <td>123.7</td>
</table>

<table>
<tr>
    <th>Target Temp</th>
    <th>Left (Fluke)</th>
    <th>Middle (Chan 0)</th>
    <th>Right (Chan 1)</th>
</tr>
<tr>
    <td>30</td>
    <td>31.4</td>
    <td>30.6</td>
    <td>30.9</td>
</tr>
<tr>
    <td>40</td>
    <td>40.2</td>
    <td>39.7</td>
    <td>40.6</td>
</tr>
<tr>
    <td>50</td>
    <td>49.1</td>
    <td>48.5</td>
    <td>50.5</td>
</tr>
<tr>
    <td>60</td>
    <td>59.4</td>
    <td>58.7</td>
    <td>61.9</td>
</tr>
<tr>
    <td>70</td>
    <td>68.9</td>
    <td>68.4</td>
    <td>72.1</td>
</tr>
<tr>
    <td>80</td>
    <td>78.8</td>
    <td>79.0</td>
    <td>83.1</td>
</tr>
<tr>
    <td>90</td>
    <td>86.7</td>
    <td>87.0</td>
    <td>91.6</td>
</tr>
<tr>
    <td>100</td>
    <td>97.0</td>
    <td>96.6</td>
    <td>103.1</td>
</tr>
<tr>
    <td>110</td>
    <td>106.2</td>
    <td>108.1</td>
    <td>113.7</td>
</tr>
<tr>
    <td>120</td>
    <td>115</td>
    <td>116.0</td>
    <td>123.1</td>
</tr>
<tr>
    <td>130</td>
    <td>120.9</td>
    <td>122.4</td>
    <td>129.4</td>
</tr>
</table>

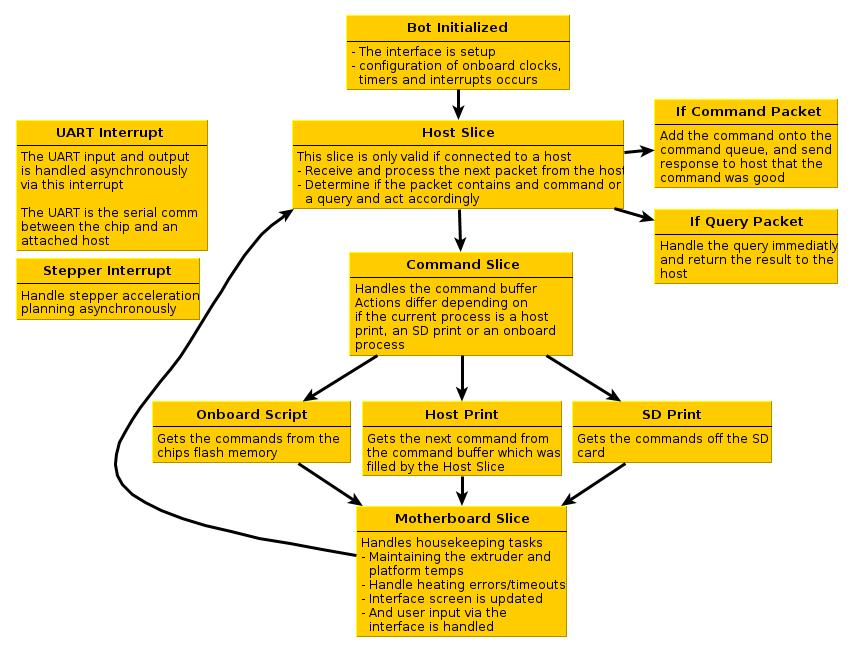
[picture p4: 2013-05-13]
docs/mightyfirmware_overview.jpg

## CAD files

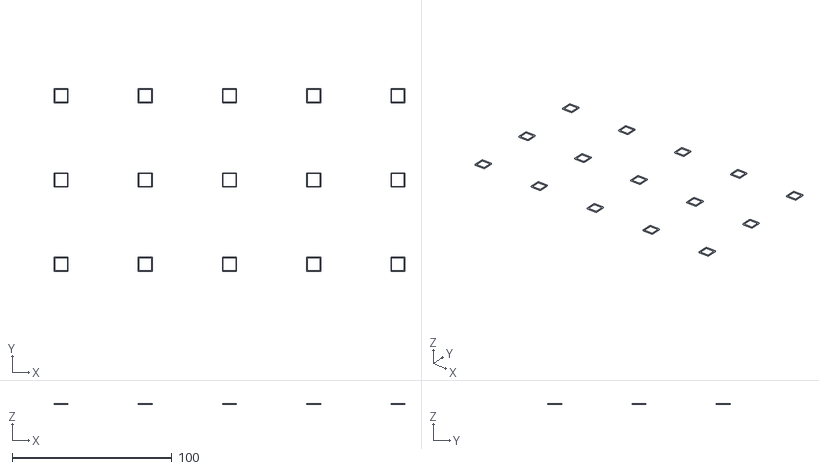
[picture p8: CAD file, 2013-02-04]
firmware/s3g scripts/PostLevelTestPrint.stl
219.9 x 114.4 x 0.713

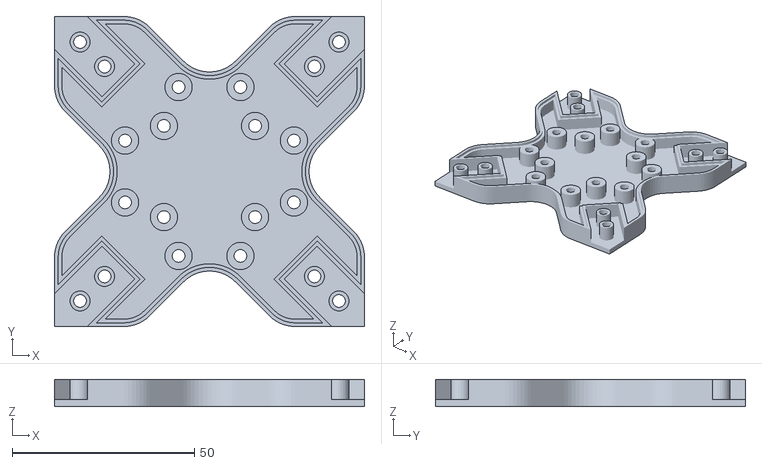
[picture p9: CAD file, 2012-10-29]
tests/test_prints/Thumping_corners_test.stl
85.0 x 85.0 x 7.50

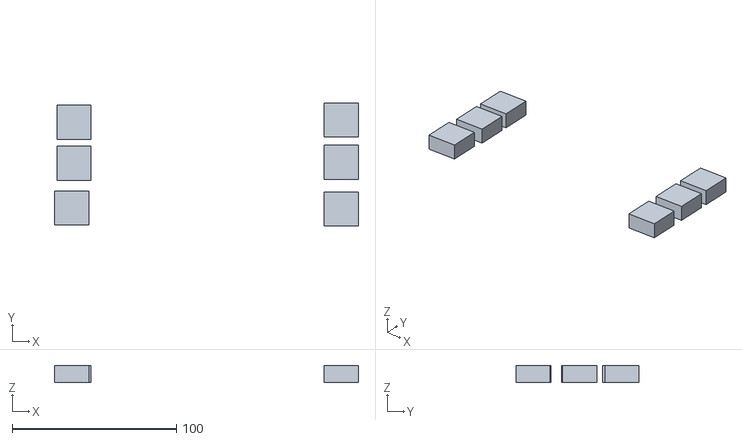
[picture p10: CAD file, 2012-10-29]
tests/test_prints/20mm_Calibration_Boxes.stl
185.3 x 75.2 x 10.5

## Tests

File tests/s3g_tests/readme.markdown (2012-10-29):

# Firmware tests

These are tests aimed at checking the compliance of the MightyBoard firmware to the s3g spec.

## Makerbot Test Explanations

### CommonFunctionTests
This suite tests any shared functions contained within Makerbottests.py

### s3gPacketTests
This suite tests the packets that are sent to the machine, and ensures the proper errors (if any) are thrown if a malformed packet is sent to a bot

### s3gSendReceiveTests
This suite tests all functions of the s3g python module, and ensures that all packets can be sent to the machine, and that the machine sends the proper response back.  These tests are pretty simple, and only involve executing the command, and asserting true if no errors are thrown (any errors that arrise will prohibit the assertion from being executed)

### s3gFunctionTests
These tests ensure that the machine processes the command correctly and takes the correct action

### s3gSDCardTests - these tests have not been verified with the current toolchain and are in draft form
This suite tests the machine operations that revolve around the SD card.  They are separate from the s3gFunctionTests because they require an SD card to be inserted into the bot.  The SD card in the bot should have the same contents of testFiles

### User Tests - these tests have not been verified with the current toolchain and are in draft form
This suite of tests requires user interaction as there is no automated process to verify correct behavior.  These tests have been beta tested once but are non verifed with the latest tool chain.

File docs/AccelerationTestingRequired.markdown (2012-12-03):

#Acceleration Testing 

## Objective
All testing up to now on acceleration has either been:
1. print based
2. logic analyzer based

We have been able to verify some aspects of our solution this way but there are important pieces we have not verified. We have JTAG now! We need to do basic verification of our algorithm against edge cases and build a chain of trust so that we can address known issues.

## Known Issues
* retraction issues
    * skipping on push back (causes gaps in filament)
    * motion must come to a full stop each time there is a retract as XY motion are zero (due to algorithm design)
* intermittent blobbing on slow to near stop - filament does not slow exactly will motor motion... pressure? 
* grinding noise on fast circles, causes jerky filament behavior
* bug : very occasional super slow segment
* bug : axes skipping - this has been reported and may be bot related, pullys or power supply (one bot known to work in one location, but not in another) But lets make sure we don't have any speed jumps beyond allowable acceleration rate
* lets review with support and the makebot operaters group to see if any other known issues have come up that I am forgetting

## Some additional Questions
* what are differences between pololu drivers and botsteps?
* how would motors / motion behave differently with non fixed stepper interrupt?
* how does filament behave with pressure?
* how do filament diameter settings change with acceleration (1 user reporting needing to change settings with update.... verify if this user is sane)
* can we make the planner faster (yes) and would this be a valuable use of time?

## Testing 
### Test Prints
* Curves at different sizes/resolutions and different speeds
* single shell box x 6 for retraction test
* high detail edges inset (inner shell)
* miracle grue vs skeinforge vs slicer prints

### Tests
1. Test that all junction speed changes proscribed by planner are > minspeedchange and < maxspeedchange
     1. test with jtag - write flag test for speed change, run test prints and stop on flag raised
     2. write speed changes to a packet and query over s3g?
     3. use PC based simulator (write or use Jetty's)
2. Test that acceleration rates are always > minrate and < maxrate
     * same possible tests here as in 1.
3. Test that speed goal and actual speed acheived by steppers are the same, or if different, below a threshold (speed junction changes are still within allowable range)
     * same possible tests here as in 1.
4. Run retraction test print at different settings (includes skeinforge settings + filament acceleration parameters)
     * this is a printing test - ie it will take many man hours
5. Grinding on fast circles....?
    1. review motor characteristics
         * looking at the revision notes on the motor datasheet, we may be over driving the motors so they cannot reach the full microstepping current levels.... verify whether this is true with moons, try running the steppers at lower vrefs
         * find expected step change time for the motor using L/R - are we stepping faster than the motor can step?  this would cause slipping.
    2. look at trapezoids generated for the circle
         * jtag - stop at each junction point around the circle
         * PC based simulator - dump trapezoids for circle
         * send trapezoid info back in s3g packet
    3. if trapezoids are OK, assess non fixed vs fixed interrupt behavior - smoothness of motion
         * PC based simulator to look at real difference in stepper pattern
         * print test with logic analyzer to view stepper pattern difference
         * sound / print quality comparison
    4. another thing to consider is the difference between stepper drivers
         * run the same print with differnt stepper drivers and asses sound / print quality differences
6. Asses fixed vs non fixed stepper interrupts
    1. how does the cpu available time compare? during fastest motion, slowest motion
         * mathematical assessment based on interrupt schedule scheme & speed range
    2. how does stepper motion smoothness compare with ideal?
         * mathematical assessment based on step schedule scheme 
    3. how does inter-stepper scheduling compare with ideal?
         * mathematical assessment based on step schedule scheme 
7. Filament speed up slow down test.....? Filament diameter tests?
    some interesting links:

    https://github.com/repetier/Repetier-Firmware/wiki/Hardware-settings-and-print-quality

    http://softsolder.com/2012/02/01/reversal-zits-extruder-pressure-vs-flow-vs-acceleration/

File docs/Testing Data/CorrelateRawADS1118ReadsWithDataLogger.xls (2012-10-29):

Data Logger Temp | Mighty Raw
27.104 | -4
27.104 | -4
27.1077 | -4
27.1077 | -4
27.1095 | -4
27.1095 | -4
27.1104 | -4
27.1104 | -4
27.1113 | -4
27.1159 | -4
27.1159 | -4
27.1178 | -4
27.1187 | -4
27.1187 | -4
27.1187 | -4
27.1196 | -4
27.1196 | -4
27.1196 | -4
27.1224 | -4
27.1224 | -4
27.1224 | -4
27.127 | -4
27.1289 | -4
27.1289 | -4
27.1289 | -4
27.1317 | -4
27.1326 | -4
27.1326 | -4
27.1326 | -4
27.1822 | -4
27.1979 | -4
27.2613 | -4
27.2613 | -3
27.3865 | -3
27.3865 | -3
27.4022 | -3
27.5448 | -3
27.5448 | -2
27.5495 | -3
27.5495 | -3
27.5652 | -3
27.568 | -3
27.5698 | -3
27.5698 | -2
27.5698 | -2
27.5781 | -3
27.5781 | -3
27.5781 | -3
27.58 | -3
27.58 | -3
27.58 | -3
27.5818 | -3
27.5818 | -3
27.5837 | -3
27.5837 | -3
27.5837 | -3
27.5837 | -3
27.5883 | -3
27.5883 | -3
27.5883 | -3
27.5938 | -3
27.6095 | -3
27.6112 | -2
27.6112 | -2
27.7226 | -2
27.7226 | -2
27.7226 | -2
27.75 | -2
27.75 | -2
27.75 | -2
27.8992 | -2
27.8992 | -1
27.9707 | -2
27.9864 | -2
28.1486 | -1
28.1486 | -1
28.1486 | -1
28.2439 | -2
28.2439 | -1
28.2439 | -1
28.4457 | 0
28.4457 | 0
28.529 | -1
28.529 | 0
28.529 | 0
28.8135 | 0
28.8135 | 1
28.8135 | 1
28.8756 | 0
28.8756 | 0
29.2224 | 2
29.2322 | 1
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

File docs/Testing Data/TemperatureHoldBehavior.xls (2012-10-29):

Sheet: Final - (re) Added PWM control
0.003087043762 | 43
0.5033061504 | 43
1.003551006 | 43
1.503797054 | 43
2.004165173 | 43
2.504424095 | 43
3.00466013 | 43
3.504907131 | 43
4.005155087 | 43
4.505398035 | 43
5.00564599 | 43
5.505897999 | 44
6.006142139 | 44
6.50642705 | 45
7.006759167 | 46
7.507004023 | 46
8.007255077 | 47
8.507502079 | 49
9.007745981 | 50
9.5081141 | 51
10.00823808 | 52
10.50850201 | 53
11.00885415 | 55
11.50911212 | 56
12.00935006 | 58
12.50960398 | 59
13.00984716 | 60
13.51009202 | 62
14.01446819 | 64
14.51880598 | 65
15.02320409 | 67
15.52344918 | 67
16.02369499 | 69
16.52408409 | 70
17.02419114 | 72
17.52456307 | 73
18.02478409 | 75
18.52502012 | 77
19.02530098 | 78
19.52555013 | 80
20.02579498 | 82
20.52601099 | 84
21.02627611 | 86
21.52654815 | 87
22.02690911 | 90
22.52715611 | 91
23.02740407 | 93
23.52765203 | 95
24.028018 | 97
24.52813911 | 98
25.02839112 | 100
25.52863812 | 101
26.02898097 | 103
26.52926207 | 104
27.02950215 | 106
27.529742 | 107
28.029984 | 108
28.53025413 | 110
29.03048801 | 111
29.53073621 | 112
30.03110313 | 114
30.53135514 | 115
31.03160119 | 117
31.53187299 | 118
32.03209114 | 120
32.53233504 | 121
33.03259206 | 123
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

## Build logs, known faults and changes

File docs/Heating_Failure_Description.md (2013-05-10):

Heating Failure Description
==========

List of all Heater Errors/Heating Failures broken down by numbers displayed during the Heating Failure! error message on the Replicator 2 and Replicator 2X.

Heating Failure #1
-----

#### Message displayed:

    "Heating Failure #1"  
    "Software Temp Limit"  
    "Reached! Please"  
    "Shutdown or Restart"  

#### Cause:

Temperature above the software predefined limit of 300 degrees C was read over a number of consecutive attempts.

#### Printer Action:

The printer should shut off the heater, cancel the print in progress, and flash lights.

Heating Failure #2
-----

#### Message displayed:

    "Heating Failure #2"  
    "My extruders are not"  
    "heating properly."  
    "Check my connections"  

#### Cause:

We have waited for the software predefined timeout of 90 seconds and did not see the temperature increase by at least 10 degrees C over a number of tries.

#### Printer Action:

The printer should shut off the heater, cancel the print in progress, and flash lights.

Heating Failure #3
-----

#### Message displayed:

    "Heating Failure #3"  
    "My extruders are"  
    "losing temperature."  
    "Check my connections"  

#### Cause:

Temperature has dropped by more than 30 degrees C after it has reached it's set target temperature.

#### Printer Action:

The printer should shut off the heater, cancel the print in progress, and flash lights.

Heating Failure #4
-----

#### Message displayed:

    "Heating Failure #4"  
    "My temperature reads"  
    "are failing! Please"  
    "Check my connections"  

#### Cause:

Thermocouple is either damaged or disconnected on one of the heaters.

#### Printer Action:

The offending heater will be shut off but the print will continue even if the offending heater is used for the print.

Heating Failure #5
-----

#### Message displayed:

    "Heating Failure #5"   
    "I'm reading out of"  
    "range temperatures."  
    "Check my connections"  

#### Cause:

Voltage read from a temperature sensor a number of consecutive times is out of the range of the voltage to temperature translation table.  Something electrical has gone wrong with any of the temperature sensors.

#### Printer Action:

The printer should shut off the heater, cancel the print in progress, and flash lights.

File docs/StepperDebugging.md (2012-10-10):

#Stepper Debugging
A document to describe how to harvest data from botsteps for stepper debugging.  Unnecessary pausing, abnormal step patterns durion various portions of prints and similar issues can be debugged using the methods described below.

##Bot Step Breakout
Analysis of the Step pins will show when a given stepper motor is being turned by the motherboard.  Solder a lead directly onto this pin, and attach a logic analyzer to it and run a print to see when this motor is stepping.

##Taking some readings
The logic analyzer of choice is the Saleae Logic Analyzer.  Saleae provide a program called Logic (www.saleae.com/downloads) to drive the analyzer.  The data gathered is displayed as a Step Graph, and can be exported to a CSV file for additional processing.  

##Interpreting Data
While information can be parsed out of data gathered with the above methodology, there are several caveats that should be respected:
    * Steps have no notion of acceleration, so attempting to find stepper velocity or build acceleration trapezoids would require modeling the actual stepper you want to look at.
The actual data collected can be visualized as a step graph using the Logic program provided by Soleae.

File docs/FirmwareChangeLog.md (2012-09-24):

# Firmware Changes Log

## Firmware 6.1 changes
* Toolhead offsets are stored entirely on the bot, removing the need for G54, G55, G10 codes.  This means that T0 has offset of 0, and T1 has offset of {33mm+/-, 0, 0} on the replicator 1 or 2X
* All eeprom values formerly stored in steps are now store in mm - this is to facilitate changing of the steps_per_mm values
* Acceleration complete rewrite.  We now use Jetty Acceleration
* EEPROM fields renamed to not use OFFSET in the titles.  These are confusing in json parsing.

## Firmware 5.6 changes
* New menu added for changing settings while printing. 
* Print time now recorded while printing.  Queryable by PC host.  Also visible on the onboard UI
* Current Line Number now visible during printing.  Line number refers to s3g command number, not gcode line number
* Total print time for the bot is stored in eeprom.  This is queryable by s3g host and is visible on the onboard UI 
* SD card menu made more robust to errors and issues cause by static discharge

## Firmware 5.5 changes

* M6 wait issue : bot handles heating the platform.  This fixes the intermittent issue where the bot stalls after the platform heats up.
* Axis Home Offsets changed : Single Extruder offsets are now: X: 152, Y: 72.  Dual extruder offsets are now: X: 152, Y: 75.   The offset refers to the distance from the center of the right nozzle.  Previous firmware used the middle point between the two nozzles as the reference point for the Dual Extruder machines.  
* Heating error sometimes causes prints to fail during long prints - changed fail counter so that it cannot overflow if there are a few bad reads over a long period of time
* Changed plate leveling script to front-back-left-right-center, changed text to say "tighten four or five times" instead of "tighten all the way"
* Nozzle calibrate script lowers the platform and heats platform first to speed heating when running the script
* Axis inversion defaults to XYZB inverted
* spacing errors fixed in some onboard bot screens
* acceleration added to bot movement
* Cooling Fan on Extruders has hysteresis to prevent turning on and off repeatedly at threshold temperature.
* z clipping added.  if move describes a point longer than the z axes, the bot will only go to max z length (z length can be changed in eeprom settings)

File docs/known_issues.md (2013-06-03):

Bot cannot read file names longer that 32 characters.  There is no warning to the user about this, the filenames just do not show up.

Bot cannot read SD cards bigger than 2 Go. A warning is issued.

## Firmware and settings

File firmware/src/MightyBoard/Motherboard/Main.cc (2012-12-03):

/*
 * Copyright 2010 by Adam Mayer	 <adam@makerbot.com>
 *
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
 * You should have received a copy of the GNU General Public License
 * along with this program.  If not, see <http://www.gnu.org/licenses/>
 */

#include "Main.hh"
#include "Host.hh"
#include "Command.hh"
#include <avr/interrupt.h>
#include <util/atomic.h>
#include <avr/wdt.h>
#include "Timeout.hh"
#include "Steppers.hh"
#include "Motherboard.hh"
#include "SDCard.hh"
#include "Eeprom.hh"
#include "EepromMap.hh"
#include "TemperatureTable.hh"
#include <util/delay.h>
#include "UtilityScripts.hh"
#include "Piezo.hh"
#ifdef STACK_PAINT
#include "Menu_locales.hh"
#endif

#define DEBUG_SRAM_MONITOR
#if defined(STACK_PAINT) && defined(DEBUG_SRAM_MONITOR)
	bool stackAlertLockout = false;
	uint16_t stackAlertCounter = 0;
#endif

#ifdef STACK_PAINT

        //Stack checking
        //http://www.avrfreaks.net/index.php?name=PNphpBB2&file=viewtopic&t=52249
        extern uint8_t _end;
        extern uint8_t __stack;

        #define STACK_CANARY 0xc5

        void StackPaint(void) __attribute__ ((naked)) __attribute__ ((section (".init1")));

        void StackPaint(void)
        {
                #if 0
                        uint8_t *p = &_end;

                        while(p <= &__stack)
                        {
                                *p = STACK_CANARY;
                                p++;
                        }
                #else
                        __asm volatile ("    ldi r30,lo8(_end)\n"
                                        "    ldi r31,hi8(_end)\n"
                                        "    ldi r24,lo8(0xc5)\n" /* STACK_CANARY = 0xc5 */
                                        "    ldi r25,hi8(__stack)\n"
                                        "    rjmp .cmp\n"
                                        ".loop:\n"
                                        "    st Z+,r24\n"
                                        ".cmp:\n"
                                        "    cpi r30,lo8(__stack)\n"
                                        "    cpc r31,r25\n"
                                        "    brlo .loop\n"
                                        "    breq .loop"::);
                #endif
        }


        uint16_t StackCount(void)
        {
                const uint8_t *p = &_end;
                uint16_t       c = 0;

                while(*p == STACK_CANARY && p <= &__stack)
                {
                        p++;
                        c++;
                }

                return c;
        }

#endif

void reset(bool hard_reset) {
	ATOMIC_BLOCK(ATOMIC_FORCEON) {
		
		bool brown_out = false;
		uint8_t resetFlags = MCUSR & 0x0f;
		// check for brown out reset flag and report if true
		if(resetFlags & (1 << 2)){
			brown_out = true;
		}
		
    // clear watch dog timer and re-enable
		if(hard_reset)
		{ 
      // ATODO: remove disable
			wdt_disable();
			MCUSR = 0x0;
			wdt_enable(WDTO_8S); // 8 seconds is max timeout
		}
		
		// initialize major classes
		Motherboard& board = Motherboard::getBoard();	
    sdcard::reset();
    Piezo::reset();
		utility::reset();
		command::reset();
		eeprom::init();
    steppers::init();
		steppers::abort();
		steppers::reset();
		board.reset(hard_reset);

	// brown out occurs on normal power shutdown, so this is not a good message		
	//	if(brown_out)
	//	{
	//		board.getInterfaceBoard().errorMessage("Brown-Out Reset     Occured", 27);
	//		board.startButtonWait();
	//	}
	}
}

int main() {

	Motherboard& board = Motherboard::getBoard();
#ifdef REVG
  INTERFACE_POWER.setDirection(true);
  INTERFACE_POWER.setValue(false);
#endif
  board.init();
	reset(true);
	sei();
	    
	while (1) {
		// Host interaction thread.
		host::runHostSlice();	
		// Command handling thread.
		command::runCommandSlice();
		// Motherboard slice
		board.runMotherboardSlice();
		//Alert if SRAM/stack has been corrupted by running out of SRAM
#if defined(STACK_PAINT) && defined(DEBUG_SRAM_MONITOR)
		stackAlertCounter ++;
		if ( stackAlertCounter >= 5000 ) {
			if (( StackCount() == 0 )) {  //( ! stackAlertLockout ) && 
        board.errorResponse(ERROR_SRAM);
				stackAlertLockout = true;
			}
			stackAlertCounter = 0;
	  }
#endif
    // check for new tones
    Piezo::runPiezoSlice();

    // reset the watch dog timer
		wdt_reset();

	}
	return 0;
}

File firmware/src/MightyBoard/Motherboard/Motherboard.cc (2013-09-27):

/*
 * Copyright 2010 by Adam Mayer	 <adam@makerbot.com>
 *
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
 * You should have received a copy of the GNU General Public License
 * along with this program.  If not, see <http://www.gnu.org/licenses/>
 */

#include <stdint.h>
#include <avr/interrupt.h>
#include <avr/io.h>
#include <util/atomic.h>
#include "Motherboard.hh"
#include "Configuration.hh"
#include "Steppers.hh"
#include "Command.hh"
#include "Interface.hh"
#include "Commands.hh"
#include "Eeprom.hh"
#include "EepromMap.hh"
#include "SoftI2cManager.hh"
#include "Piezo.hh"
#include "RGB_LED.hh"
#include "Errors.hh"
#include <avr/eeprom.h>
#include <util/delay.h>
#include "Menu_locales.hh"
#include "TemperatureTable.hh"

#ifndef JKN_ADVANCE
    #warning "Release: JKN_ADVANCE disabled in Configuration.hh"
#endif

/// Instantiate static motherboard instance
Motherboard Motherboard::motherboard;

enum HeaterTypes{
	EXTRUDER_A = 0,
	EXTRUDER_B = 1,
	HEATER_HBP = 2,
};

/// Create motherboard object
Motherboard::Motherboard() :
			lcd(LCD_STROBE, LCD_DATA, LCD_CLK),
			interfaceBoard(buttonArray, lcd),
			platform_thermistor(PLATFORM_PIN, TemperatureTable::table_thermistor),
			platform_heater(platform_thermistor,platform_element,SAMPLE_INTERVAL_MICROS_THERMISTOR,
			eeprom_offsets::T0_DATA_BASE + toolhead_eeprom_offsets::HBP_PID_BASE, false, HEATER_HBP),
			using_platform(eeprom::getEeprom8(eeprom_offsets::HBP_PRESENT, 1)),
#ifdef MODEL_REPLICATOR2
			Extruder_One(0, EXA_PWR, EXA_FAN, ThermocoupleReader::CHANNEL_ONE, eeprom_offsets::T0_DATA_BASE),
			Extruder_Two(1, EXB_PWR, EXB_FAN, ThermocoupleReader::CHANNEL_TWO, eeprom_offsets::T1_DATA_BASE),
			therm_sensor(THERMOCOUPLE_DO,THERMOCOUPLE_SCK,THERMOCOUPLE_DI, THERMOCOUPLE_CS)		
#else
	Extruder_One(0, EX1_PWR, EX1_FAN, THERMOCOUPLE_CS1,eeprom_offsets::T0_DATA_BASE),
	Extruder_Two(1, EX2_PWR, EX2_FAN, THERMOCOUPLE_CS2,eeprom_offsets::T1_DATA_BASE)
#endif
{
}

 
#define ENABLE_TIMER_INTERRUPTS     TIMSK2 |= (1<<OCIE2A); \
                            TIMSK5 |= (1<<OCIE5A)
 
#define DISABLE_TIMER_INTERRUPTS    TIMSK2 &= ~(1<<OCIE2A); \
                            TIMSK5 &= ~(1<<OCIE5A)
 

void Motherboard::init(){
	SoftI2cManager::getI2cManager().init();

	// Check if the interface board is attached
	hasInterfaceBoard = interface::isConnected();

	micros = 0;
	initClocks();

	// Configure the debug pins.
	DEBUG_PIN.setDirection(true);
	DEBUG_PIN1.setDirection(true);
	DEBUG_PIN2.setDirection(true);
	DEBUG_PIN3.setDirection(true);	
	DEBUG_PIN4.setDirection(true);
	DEBUG_PIN5.setDirection(true);
	DEBUG_PIN6.setDirection(true);
		
#ifdef MODEL_REPLICATOR2 
	therm_sensor.init();
	therm_sensor_timeout.start(THERMOCOUPLE_UPDATE_RATE);
#else
	cutoff.init();
	extruder_manage_timeout.start(SAMPLE_INTERVAL_MICROS_THERMOCOUPLE);
#endif

	// initialize the extruders
	Extruder_One.reset();
	Extruder_Two.reset();
    
	HBP_HEAT.setDirection(true);
	platform_thermistor.init();
	platform_heater.reset();
	platform_timeout.start(SAMPLE_INTERVAL_MICROS_THERMISTOR);

}

void Motherboard::initClocks(){

	// set up piezo timer
	Piezo::shutdown_timer();
		
	// Reset and configure timer 5,  stepper
	// interrupt timer.
	TCCR5A = 0x00;
	TCCR5B = 0x0A; // no prescaling
	TCCR5C = 0x00;
	OCR5A = 0x2000; //INTERVAL_IN_MICROSECONDS * 16;
	TIMSK5 = 0x02; // turn on OCR5A match interrupt
	
	// Reset and configure timer 2, the microsecond timer, advance_timer and debug LED flasher timer.
	TCCR2A = 0x02; //CTC  //0x00;  
	TCCR2B = 0x04; //prescaler at 1/64  //0x0A; /// prescaler at 1/8
	OCR2A = 25; //Generate interrupts 16MHz / 64 / 25 = 10KHz  //INTERVAL_IN_MICROSECONDS;  // TODO: update PWM settings to make overflowtime adjustable if desired : currently interupting on overflow
	OCR2B = 0;
	TIMSK2 = 0x02; // turn on OCR2A match interrupt

#ifdef MODEL_REPLICATOR2
	// reset and configure timer 3, the Extruders timer
	// Mode: Fast PWM with TOP=0xFF (8bit) (WGM3:0 = 0101), cycle freq= 976 Hz
	// Prescaler: 1/64 (250 KHz)
	TCCR3A = 0b00000001;  
	TCCR3B = 0b00001011; /// set to PWM mode
	OCR3A = 0;
	OCR3C = 0;
	TIMSK3 = 0b00000000; // no interrupts needed
#else
	// reset and configure timer 1, the Extruder Two PWM timer
	// Mode: Fast PWM with TOP=0xFF (8bit) (WGM3:0 = 0101), cycle freq= 976 Hz
	// Prescaler: 1/64 (250 KHz)
	TCCR1A = 0b00000001;  
	TCCR1B = 0b00001011; /// set to PWM mode
	OCR1A = 0;
	OCR1B = 0;
	TIMSK1 = 0b00000000; // no interrupts needed
  
	// reset and configure timer 4, the Extruder One PWM timer
	// Mode: Fast PWM with TOP=0xFF (8bit) (WGM3:0 = 0101), cycle freq= 976 Hz
	// Prescaler: 1/64 (250 KHz)
	TCCR4A = 0b00000001;  
	TCCR4B = 0b00001011; /// set to PWM mode
	OCR4A = 0;
	OCR4B = 0;
	TIMSK4 = 0b00000000; // no interrupts needed
#endif
}

#define ONE_MINUTE 60000000
#define ONE_SECOND 1000000
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

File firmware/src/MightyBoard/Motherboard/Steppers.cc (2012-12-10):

/*
 * Copyright 2010 by Adam Mayer	 <adam@makerbot.com>
 *
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
 * Modifications for Jetty Marlin compatability, authored by Dan Newman and Jetty.
 */

#ifndef SIMULATOR

#define __STDC_LIMIT_MACROS
#include "Steppers.hh"
#include "StepperAxis.hh"
#include <stdint.h>
#include <util/delay.h>
#include "Eeprom.hh"
#include "EepromMap.hh"
#include "stdio.h"

#else

#include "Steppers.hh"
#include "StepperAxis.hh"
#include <stdint.h>
#include "Eeprom.hh"
#include "EepromMap.hh"

#ifdef ATOMIC_BLOCK
#undef ATOMIC_BLOCK
#endif
#define ATOMIC_BLOCK(x)

#ifdef labs
#undef labs
#endif
#define labs(x) abs(x)

#define st_init()
#define st_interrupt() false
#define st_extruder_interrupt()
#define quickStop()
#define DEBUG_TIMER_TCTIMER_USI 0
#define DEBUG_TIMER_START
#define DEBUG_TIMER_FINISH

#endif

#ifdef DEBUG_ONSCREEN
	volatile float debug_onscreen1 = 0.0, debug_onscreen2 = 0.0;
#endif

namespace steppers {

#ifndef SIMULATOR

/// Set up the digipot pins 
DigiPots digi_pots[STEPPER_COUNT] = {
        DigiPots(X_POT_PIN, eeprom_offsets::DIGI_POT_SETTINGS),
        DigiPots(Y_POT_PIN, eeprom_offsets::DIGI_POT_SETTINGS),
        DigiPots(Z_POT_PIN, eeprom_offsets::DIGI_POT_SETTINGS),
        DigiPots(A_POT_PIN, eeprom_offsets::DIGI_POT_SETTINGS),
        DigiPots(B_POT_PIN, eeprom_offsets::DIGI_POT_SETTINGS),
};

#else

typedef struct {
	void (*init)(int);
	void (*setPotValue)(uint8_t);
} DigiPots;

static void dummy_init(int i) { (void)i; }
static void dummy_setPotValue(uint8_t v) { (void)v; }

DigiPots digi_pots[STEPPER_COUNT] = {
	{dummy_init, dummy_setPotValue},
	{dummy_init, dummy_setPotValue},
	{dummy_init, dummy_setPotValue},
	{dummy_init, dummy_setPotValue},
	{dummy_init, dummy_setPotValue}
};

#endif

void initPots(){
	// set digi pots to stored default values
	for ( int i = 0; i < STEPPER_COUNT; i++ ) {
		digi_pots[i].init(i);
	}
}

volatile bool is_running;
volatile bool is_homing;
bool acceleration = true;
uint8_t plannerMaxBufferSize;
FPTYPE axis_steps_per_unit_inverse[STEPPER_COUNT];

// Segments are accelerated when segmentAccelState is true; unaccelerated otherwise
static bool segmentAccelState = true;

bool holdZ = false;

bool z_homing = false;
uint8_t z_homed = 0;

Point tolerance_offset_T0;
Point tolerance_offset_T1;
Point *tool_offsets;
uint8_t toolIndex = 0;

//Also requires DEBUG_ONSCREEN to be defined in StepperAccel.h
//#define TIME_STEPPER_INTERRUPT

#if defined(DEBUG_ONSCREEN) && defined(TIME_STEPPER_INTERRUPT)
uint16_t debugTimer = 0;
#endif


bool isRunning() {
	return is_running || is_homing;
}


void loadToleranceOffsets() {
	// get toolhead offsets
	ATOMIC_BLOCK(ATOMIC_RESTORESTATE){
		for(int i = 0; i  < 3; i++){
			int32_t tolerance_err = (int32_t)(((float)((int32_t)eeprom::getEeprom32(eeprom_offsets::TOOLHEAD_OFFSET_SETTINGS_MM + i*4, 0) * stepperAxisStepsPerMM(i))) / 1000);
			tolerance_offset_T1[i] = tolerance_err;
		}
		// For now, force Z offset to be zero as bad things can happen if it has a value AND there is no use case for it having a value on the replicator
		// extruder axes are 0 because offset concept does not apply
		for (int i = 2; i < STEPPER_COUNT; i++)
			tolerance_offset_T1[i] = 0;

		for(int i = 0; i < STEPPER_COUNT; i++)
			tolerance_offset_T0[i] = 0;
	}
}


void reset() {
	stepperAxisInit(false);

	initPots();

  // these variables help us to track z stage lowering, so we can do smart cancel build behavior
  z_homed = 0;
  z_homing = false;

	loadToleranceOffsets();
	changeToolIndex(0);

	// If acceleration has not been initialized before (i.e. last time we ran we were an earlier firmware),
	// then we initialize the acceleration eeprom settings here
	uint8_t accelerationStatus = eeprom::getEeprom8(eeprom_offsets::ACCELERATION_SETTINGS + acceleration_eeprom_offsets::DEFAULTS_FLAG, 0xFF);
	if (accelerationStatus !=  _BV(ACCELERATION_INIT_BIT)) {
		eeprom::setDefaultsAcceleration();
	}

        //Get the acceleration settings
	uint8_t accel = eeprom::getEeprom8(eeprom_offsets::ACCELERATION_SETTINGS + acceleration_eeprom_offsets::ACCELERATION_ACTIVE, 0) & 0x01;
        acceleration = accel & 0x01;

	setSegmentAccelState(acceleration);
	deprimeEnable(true);

	//Here's more documentation on the various settings / features
	//http://wiki.ultimaker.com/Marlin_firmware_for_the_Ultimaker
	//https://github.com/ErikZalm/Marlin/commits/Marlin_v1
	//http://forums.reprap.org/read.php?147,94689,94689
	//http://reprap.org/pipermail/reprap-dev/2011-May/003323.html
	//http://www.brokentoaster.com/blog/?p=358

	for ( uint8_t i = 0; i < STEPPER_COUNT; i ++ )
		axis_steps_per_unit_inverse[i] = FTOFP(1.0 / stepperAxisStepsPerMM(i));

	//Macros to clean things up a bit
	#define NAC1(LOCATION) eeprom_offsets::ACCELERATION_SETTINGS + acceleration_eeprom_offsets::LOCATION
	#define NAC2(LOCATION) eeprom_offsets::ACCELERATION2_SETTINGS + acceleration2_eeprom_offsets::LOCATION
	#define AC1(LOCATION,INT16INDEX) NAC1(LOCATION) + sizeof(uint16_t) * INT16INDEX
	#define AC2(LOCATION,INT16INDEX) NAC2(LOCATION) + sizeof(uint16_t) * INT16INDEX

	// Set max acceleration in units/s^2 for print moves
	// X,Y,Z,A,B maximum start speed for accelerated moves.
	// A,B default values are good for skeinforge 40+, for older versions raise them a lot.
	max_acceleration_units_per_sq_second[X_AXIS] = (uint32_t)eeprom::getEeprom16(AC1(MAX_ACCELERATION_AXIS,0), DEFAULT_MAX_ACCELERATION_AXIS_X);
	max_acceleration_units_per_sq_second[Y_AXIS] = (uint32_t)eeprom::getEeprom16(AC1(MAX_ACCELERATION_AXIS,1), DEFAULT_MAX_ACCELERATION_AXIS_Y);
	max_acceleration_units_per_sq_second[Z_AXIS] = (uint32_t)eeprom::getEeprom16(AC1(MAX_ACCELERATION_AXIS,2), DEFAULT_MAX_ACCELERATION_AXIS_Z);
	max_acceleration_units_per_sq_second[A_AXIS] = (uint32_t)eeprom::getEeprom16(AC1(MAX_ACCELERATION_AXIS,3), DEFAULT_MAX_ACCELERATION_AXIS_A);
	max_acceleration_units_per_sq_second[B_AXIS] = (uint32_t)eeprom::getEeprom16(AC1(MAX_ACCELERATION_AXIS,4), DEFAULT_MAX_ACCELERATION_AXIS_B);

	for (uint8_t i = 0; i < STEPPER_COUNT; i ++) {
		// Limit the max accelerations so that the calculation of block->acceleration & JKN Advance K2
		// can be performed without overflow issues
		if (max_acceleration_units_per_sq_second[i] > (uint32_t)((float)0xFFFFF / stepperAxisStepsPerMM(i)))
		     max_acceleration_units_per_sq_second[i] = (uint32_t)((float)0xFFFFF / stepperAxisStepsPerMM(i));
		axis_steps_per_sqr_second[i] = (uint32_t)((float)max_acceleration_units_per_sq_second[i] * stepperAxisStepsPerMM(i));
		axis_accel_step_cutoff[i] = (uint32_t)0xffffffff / axis_steps_per_sqr_second[i];
	}

	//Set default acceleration for "Normal Moves (acceleration)" and "filament only moves (retraction)" in mm/sec^2

	// X,Y,Z,A,B max acceleration in mm/s^2 for printing moves
	p_acceleration = (uint32_t)eeprom::getEeprom16(NAC1(MAX_ACCELERATION_NORMAL_MOVE), DEFAULT_MAX_ACCELERATION_NORMAL_MOVE);
	if (p_acceleration > 10000)
	     // 10,000 limit is actually a little smaller than 0xFFFFF / 96 steps/mm
	     p_acceleration = 10000;
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

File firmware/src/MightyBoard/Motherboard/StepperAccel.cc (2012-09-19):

/*
  StepperAccel.cc - stepper motor driver: executes motion plans using stepper motors
  Part of Grbl

  Copyright (c) 2009-2011 Simen Svale Skogsrud

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
  The timer calculations of this module informed by the 'RepRap cartesian firmware' by Zack Smith
  and Philipp Tiefenbacher.

  This module has been heavily modified from the original Marlin (https://github.com/ErikZalm).
  JKN Advance, YAJ (Yet Another Jerk), Advance Pressure Relax and modifications originate from
  Jetty Firmware (https://github.com/jetty840/G3Firmware).  These modifications and features are
  copyrighted and authored by Dan Newman and Jetty under GPL.  Copyright (c) 2012.
*/


#include "Configuration.hh"
#include "StepperAccel.hh"

#ifdef LOOKUP_TABLE_TIMER
	#include "StepperAccelSpeedTable.hh"
#endif

#include "Motherboard.hh"

#include <avr/interrupt.h>
#include <string.h>
#include <math.h>
#include "StepperAxis.hh"
#include "Steppers.hh"


block_t		*current_block;				// A pointer to the block currently being traced
int16_t		extruder_deprime_steps[EXTRUDERS];	// Positive number of steps to prime / deprime
bool		extrude_when_negative[EXTRUDERS];	// True if negative values cause an extruder to extrude material
float		extruder_only_max_feedrate[EXTRUDERS];

#ifdef JKN_ADVANCE
	enum AdvanceState {
		ADVANCE_STATE_ACCEL = 0,
		ADVANCE_STATE_PLATEAU,
		ADVANCE_STATE_DECEL
	};
	static enum AdvanceState	advance_state;
	static int32_t			advance_pressure_relax_accumulator;
	#ifdef JKN_ADVANCE_LEAD_DE_PRIME
		static int16_t		lastAdvanceDeprime[EXTRUDERS];
	#endif

	#define ADVANCE_INTERRUPT_FREQUENCY 10000	// 10KHz

	static uint8_t			st_extruder_interrupt_rate[EXTRUDERS]		= {0, 0};
	static uint8_t			extruder_interrupt_steps_per_call[EXTRUDERS]	= {0, 0};
	static uint8_t			st_extruder_interrupt_rate_counter[EXTRUDERS];
#endif

static unsigned char		out_bits;		// The next stepping-bits to be output
volatile static uint32_t	step_events_completed;	// The number of step events executed in the current block

static int32_t		acceleration_time, deceleration_time;
static uint16_t		acc_step_rate, step_rate;
static char		step_loops, step_loops_nominal;
static uint16_t		OCR5A_nominal;

static bool		deprimed[EXTRUDERS];

static bool		deprime_enabled;		//If true, depriming is On, if not, it's Off.  It's normally switched on.
							//But is switched off when loading/unloading the extruder 
static uint8_t		last_active_toolhead = 0;

#if  defined(DEBUG_TIMER)
	uint16_t debugTimer;
#endif

#ifdef OVERSAMPLED_DDA
	uint8_t oversampledCount = 0;
#endif


// intRes = intIn1 * intIn2 >> 16
// uses:
// r26 to store 0
// r27 to store the byte 1 of the 24 bit result
#define MultiU16X8toH16(intRes, charIn1, intIn2)	\
	asm volatile (					\
		"clr r26 \n\t"				\
		"mul %A1, %B2 \n\t"			\
		"movw %A0, r0 \n\t"			\
		"mul %A1, %A2 \n\t"			\
		"add %A0, r1 \n\t"			\
		"adc %B0, r26 \n\t"			\
		"lsr r0 \n\t"				\
		"adc %A0, r26 \n\t"			\
		"adc %B0, r26 \n\t"			\
		"clr r1 \n\t"				\
		:					\
		"=&r" (intRes)				\
		:					\
		"d" (charIn1),				\
		"d" (intIn2)				\
		:					\
		"r26"					\
	)

// intRes = longIn1 * longIn2 >> 24
// uses:
// r26 to store 0
// r27 to store the byte 1 of the 48bit result
#define MultiU24X24toH16(intRes, longIn1, longIn2)	\
	asm volatile (					\
		"clr r26 \n\t"				\
		"mul %A1, %B2 \n\t"			\
		"mov r27, r1 \n\t"			\
		"mul %B1, %C2 \n\t"			\
		"movw %A0, r0 \n\t"			\
		"mul %C1, %C2 \n\t"			\
		"add %B0, r0 \n\t"			\
		"mul %C1, %B2 \n\t"			\
		"add %A0, r0 \n\t"			\
		"adc %B0, r1 \n\t"			\
		"mul %A1, %C2 \n\t"			\
		"add r27, r0 \n\t"			\
		"adc %A0, r1 \n\t"			\
		"adc %B0, r26 \n\t"			\
		"mul %B1, %B2 \n\t"			\
		"add r27, r0 \n\t"			\
		"adc %A0, r1 \n\t"			\
		"adc %B0, r26 \n\t"			\
		"mul %C1, %A2 \n\t"			\
		"add r27, r0 \n\t"			\
		"adc %A0, r1 \n\t"			\
		"adc %B0, r26 \n\t"			\
		"mul %B1, %A2 \n\t"			\
		"add r27, r1 \n\t"			\
		"adc %A0, r26 \n\t"			\
		"adc %B0, r26 \n\t"			\
		"lsr r27 \n\t"				\
		"adc %A0, r26 \n\t"			\
		"adc %B0, r26 \n\t"			\
		"clr r1 \n\t"				\
		:					\
		"=&r" (intRes)				\
		:					\
		"d" (longIn1),				\
		"d" (longIn2)				\
		:					\
		"r26" , "r27"				\
	)

// Some useful constants

#define ENABLE_STEPPER_DRIVER_INTERRUPT()	TIMSK5 |= (1<<OCIE5A)
#define DISABLE_STEPPER_DRIVER_INTERRUPT()	TIMSK5 &= ~(1<<OCIE5A)


//         __________________________
//        /|                        |\     _________________         ^
//       / |                        | \   /|               |\        |
//      /  |                        |  \ / |               | \       s
//     /   |                        |   |  |               |  \      p
//    /    |                        |   |  |               |   \     e
//   +-----+------------------------+---+--+---------------+----+    e
//   |               BLOCK 1            |      BLOCK 2          |    d
//
//                           time ----->
// 
//  The trapezoid is the shape the speed curve over time. It starts at block->initial_rate, accelerates 
//  first block->accelerate_until step_events_completed, then keeps going at constant speed until 
//  step_events_completed reaches block->decelerate_after after which it decelerates until the trapezoid generator is reset.
//  The slope of acceleration is calculated with the leib ramp alghorithm.

struct lookup_table_entry {
	union {
		uint32_t dword_entry;
		uint16_t word_entry[2];
	};
};



// Shift by 1 byte to the right
#define SHIFT1(x) (uint8_t)(x >> 8 )
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

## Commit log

2012-02-01 motor_test hex file
2012-02-03 heater test script beta
2012-02-06 fixed extruder load function
    [Diagnostics.cc]
2012-06-22 fixed VID/PID of MightyBoard getting into Release branch. :(
2012-09-17 updated Stepper files with new code from jetty - this build still has some broken pieces, but printing is smooth
    [Command.cc, StepperAccel.cc, StepperAccelPlanner.cc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]
2012-09-19 reset error fixed - timer initialization OK
    [ExtruderBoard.cc, Main.cc, Menu.cc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]
2012-09-21 cancel and sleep working, some issue with spurious host loop sticking
    [Command.cc, ExtruderBoard.cc, Host.cc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]
2012-09-21 Fixed pin error for RevG, a couple more SRAM changes
    [Main.cc, Motherboard.cc]
2012-09-23 only initialize thermocouple chip on hard reset to avoid showing initializing reads after soft reset
    [Motherboard.cc]
2012-09-24 removing eeprom headers for things we are not currently using
2012-09-25 don't count "." files, menu scroll up and down work, fix new bug in cancel
    [Menu.cc]
2012-09-25 added motherboard status for waiting for button
2012-09-26 fixed toolhead offsets bug
    [Command.cc, Host.cc, Menu.cc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]
2012-09-26 Enforced multiple error message for the SD card static fail. In case there are momentary false positives
    [Command.cc, Host.cc]
2012-09-26 versioning added for changed command chain
2012-10-06 SRAM reduction : don't use SD card STABILITY_MODE
    [Command.cc, Main.cc, Menu.cc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]
2012-10-09 nozzleCalibration script update
2012-10-09 fix vibration above 1cm issue
    [Command.cc]
2012-10-10 Added Stepper Debugging doc
2012-10-10 updated calibrate nozzle script
2012-10-10 added command unpause in reset
    [Host.cc]
2012-10-16 update french language build, fix build cancel over response
    [Host.cc]
2012-10-16 fix for new bug in cancel build menu
    [Menu.cc]
2012-10-28 finished constraint commenting on eeprom fan turns off during sleep -untested filament heat temps tagged to preheat settings - untested fixed level plate script for replicator 2
    [Command.cc, Menu.cc]
2012-10-28 fix level plate script for replicator 2
2012-10-29 fixed nozzle plate script for replicator one
    [20mm_Calibration_Boxes.stl, ConfiguringApps.txt, CorrelateRawADS1118ReadsWithDataLogger.xls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]
2012-10-29 added replicator 2 nozzle script
2012-10-30 fan behavior updates, build percent handled in queue
2012-10-30 rep2 nozzle calibration scripts
2012-10-31 fix printing from left extruder with makerware
2012-11-01 nozzle calibrate script for rep2X, minor eeprom edits
2012-11-01 calibrate nozzles script fix
    [Menu.cc]
2012-11-02 fix for left extruder restart after cold pause
    [Command.cc]
2012-11-26 Updated pause behavior * Change Filament and Cold Pause cannot be executed until printer has homed
2012-11-26 Wait For Homing Msg if Z axis hasnt homed...
2012-11-29 preliminary heat process changes
2012-11-30 heaters are not shutdown on reset unless the "restart_timeout" is set to zero. for starting prints, heaters are reset when an extruder temperature command is recieved, thus the reset will be invisibl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
    [Command.cc, Motherboard.cc]
2012-11-30 Added a menu item to change the heater timeout after cancel extruder heaters are not shutdown in the filament load/unload scripts until the user exits the filament menu if preheat is on, extruder hea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
2012-11-30 added TOOLHEAD_OFFSET_SETTINGS_MM
2012-12-03 a working 2X Calibrate Nozzle Script. Incomplete changes to Toolhead offset handling
2012-12-03 update thermistor table for Replicator2X revert debugging changes in stepper handling
    [Command.cc, Steppers.cc, TemperatureTable.cc]
2012-12-03 added defineHomePosition to solve offset issue when homing after declaring toolhead 1
    [Command.cc, Steppers.cc]
2012-12-03 speed up load filament scripts so that filament tensioning is easier minor fixes to dave_fixes branch remove the enable/disable commands during buffered printin
    [Command.cc, Host.cc, Menu.cc]
2012-12-03 added Sailfish fix to slowdown code
    [Menu.cc, StepperAccelPlanner.cc]
2012-12-03 piezo pin set to zero on reset - we don't want resets during songs to lead to buzzer pin staying high forever
2012-12-07 Modify how the SDMenu screen is drawn * We reverse the list so newer items are drawn first
    [Menu.cc]
2012-12-10 update preheat reset to not clear when printing from Makerware
    [Motherboard.cc]
2012-12-10 multiple small fixes: add an abort function to heaters to allow reset without setting curret temp to 0 make slowdown_limit for usb printing double that for printing with SD card change preheat menu b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
    [Command.cc, Menu.cc, Steppers.cc]
2012-12-10 update filament load/unload text update sleep behavior bump version number
2012-12-10 Added new table for thermistor changes
2012-12-11 use abort function in heater.cc instead of reset at beginning of printing fixes two bugs
    [Command.cc]
2012-12-11 Fixed thermistor table
2012-12-11 Updated plate leveling script for the Rep2X
2012-12-11 Updateed Rep2 Plate Leveling Script
2012-12-11 Put new level plate script into Menu_locales
2013-01-17 changed text to 'filament' from 'plastic' in the startup script
2013-01-28 updated text for the 2X bot s3g support removed due to customer confusion Build time eeprom reset changed to work in "reset to factory"
    [Menu.cc]
2013-01-28 fix the calibrate nozzles script
2013-01-31 Added post plate leveling test script w/dummy plate level print
2013-01-31 Added homing to the beginning of the level build plate script
2013-01-31 Adding post level print + original stl
    [PostLevelTestPrint.STL]
2013-02-01 Added post leveling test print, with support for both HBP and Non-HBP bots
2013-02-03 fixed level plate scipts so that they return to utilities menu modify level plate scripts so use "plate" instead of "platform" s3g files are not yet up to date
    [Host.cc, Menu.cc]
2013-02-04 fixed Replicator 1 build script text fixed Replicator 2 dual and single scripts not the same length added handling of LevelTestPrint for Rep1
    [PostLevelTestPrint.stl]
2013-02-04 fix bad build flag on unload filament script fix missing space in unload message
2013-02-04 fix for "retry" level build plate with new home first script
    [Menu.cc]
2013-02-04 Updated 'current-version.txt' and updated dist with 7.1.2 hex files
2013-02-05 Added extra logic for x axis offset setting
2013-02-06 renamed plate leveling scripts to match the non localized ones
2013-03-19 Reverting 8u2 back to a previous working version
    [Makerbot-usbserial.c, Makerbot-usbserial.h]
2013-03-19 Adding a working RevH 8u2 bootloader w/ RevG PID
2013-04-09 Changing RevH PID to B016
2013-05-02 Command.cc: - Whitespace fixes - Changed behaviour of VREF when sleeping. VREF stays at normal value when in Change Filament mode to help prevent print head movement, in an effort to resume printing 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
    EepromMap.hh:
    - Added STOP_HEIGHT_VALUE location to the EEPROM Map used for Filament Change Stop Height settings.
    - Moved FREE_EEPROM_STARTS value out to account for the addition of STOP_HEIGHT_VALUE.
    EepromMap.cc:
    - Added default value writes for Filament Change Stop Height feature.
    Host.cc:
    - Whitespace fixes.
    StepperAccellPlanner.hh:
    - Added function descriptions and declarations for setting and getting Filament Change Stop Height enable var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
    [Command.cc, Host.cc, Menu.cc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]
2013-05-06 Whitespace fixes, changes and corrections to the menu structure and text.
    [Menu.cc]
2013-05-08 current_version.txt: * Added description of 7.3.2 and 7.3.1 firmware releases
    Motherboard.cc:
    * Whitespace fixes
    * Changed error handling behaviour, more heater errors will cause the print to be aborted
    * Added heater errors
    ThermocoupleDual.cc:
    * Changed error reporting algorithm, error codes are now returned and temperature value is passed by reference
    * Added error codes for communication error with the ADC chip
    ThermocoupleReader.hh:
    * Changed error reporting algorithm, error codes are now returned and temperature value is passed by reference
    * Whitespace fixes
    ThermocoupleReader.cc:
    * Changed error reporting algorithm, error codes are now returned and temperature value is pa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
    [Menu.cc, Motherboard.cc, TemperatureTable.cc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]
2013-05-08 Update Heating_Failure_Description.md
    Added all current heater errors/Heating Failures as well as their causes and printer actions.
2013-05-08 Fixed numbering of Heating Failure messages
2013-05-09 Fixed issue preventing the printer from checking for extruders not heating properly. Added timeout (15 minutes) to change filament command which results in the printer going to sleep.
    [Command.cc]
2013-05-10 fixes to z pause height screen order : Warning Stack Trace is on in this build
    [ButtonArray.cc, Menu.cc, StepperAccelPlanner.cc]
2013-05-10 removed config check in ThermocoupleReader updated error handling to use enums in ThermocoupleReader Minor modifications to ThermocoupleTable for clarity Minor modifications to Command.cc for clarity
    [ButtonArray.cc, Command.cc, Motherboard.cc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]
2013-05-10 Added hex files for mighty one and mighty two boards
2013-05-13 Changed behaviour of Z Pause Height, it now goes into active build menu instead of change filament menu.
2013-05-13 Fixed bug preventing user from restarting build after timing out of the Change Filament menu. Fixed bug that caused the Z Pause Height enable flag from beight reset when Z Pause Height Condition is r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
    [Command.cc, StepperAccelPlanner.cc]
2013-05-13 Adding overview flowchart of firmware
2013-05-14 re-fix screen order for z pause behavior
    [StepperAccelPlanner.cc]
2013-05-14 Fixed JIRA bug MW-952. Following a mid-print filament change, the 'Resume Build' item is still available on the menu.
    [Menu.cc]
2013-05-14 Fixed JIRA bug MW-946. When the printer is in the paused state and the user presses 'Back to Monitor', the print resumes.
    [Menu.cc]
2013-05-14 Adding Z stage lowering before first move of Rep2/X leveling script
2013-05-15 Updated current_version.txt to include latestversion information and added hex files for this version.
2013-05-15 continue fix for SD card build screen order
    [Host.cc]
2013-05-15 SD card prints now return to SD card menu after the Build Finished screen
2013-05-22 Fix uppercase problem
    [PostLevelTestPrint.STL]
2013-05-23 Adding seperate revH 8u2 firmware for Rep2 vs 2X, Rep2 PID = B016, Rep2X PID = B017
2013-05-23 Rep2X revH PID is B017, Adding 8u2 revH hex files to dist
2013-05-24 fixed heating bar bug updated z pause height behavior
    [StepperAccelPlanner.cc, ThermocoupleReader.cc]
2013-05-31 fix for heating up display error. changed HBP update rate to 500ms
    [ThermocoupleReader.cc]
2013-06-04 Fix two-digit hour display while printing Fix some overriden characters in French translation
    [Menu.cc]
2013-06-26 MW-1057: Changed ButtonArray pin intialization to not set some pins as outputs
2013-07-08 updating current_version.txt to 7.4.1
2013-07-09 specific argument is now case insensitive
2013-08-01 Initial changes for single filament loading during Rep2X script
2013-09-05 Initial heat hold fix
    [Host.cc, Motherboard.cc]
2013-09-05 clear user_input_timeout everytime a heat_hold or user_input timeout elapses
2013-09-05 MW-1099, Made ERROR_BOT_TYPE more abiguous
    [Command.cc]
2013-09-07 MW-1173, Fix for firmware 'unattaching' from build when bot type error occurs
    [Motherboard.cc]
2013-09-09 updating current_version.txt
2013-09-10 Fix for heat hold timeout, interrupting filament loading post cancelled build, as well as during any other onboard process
    [Menu.cc, Motherboard.cc]
2013-09-10 updated current_version and 7.5.2 dist
2013-09-13 Another change to have heat hold behave correctly in all scenarios
    [Command.cc, Host.cc, Motherboard.cc]
2013-09-13 Making Rep2X start script more clear on what extruder is being loaded
2013-09-15 MW-1135, Unpause heaters if they are still paused after a print
2013-09-25 Minor fixup in time display
    [Menu.cc]
2013-09-27 MW-1419: for Fix for change filament timeouts ending in non-resumable prints
    [Command.cc, Motherboard.cc]
2013-09-30 Reverting cursor position for build time displaying
    [Menu.cc]
2014-05-20 PID loop I term set to .75
2014-05-20 update current_version
2014-05-20 updated current_version
    Conflicts:
    firmware/current_version.txt
2014-05-20 7.5.10: Modified PID loop values (basically retuned the loop), max error accumulation set to 512, pid bypass delta set to 10 (instead of 25)
    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
2014-05-20 Messing with the PID loop values some more
2014-08-26 MW-4347: Updating PID loop default value defines to be determined based on the model type of the build

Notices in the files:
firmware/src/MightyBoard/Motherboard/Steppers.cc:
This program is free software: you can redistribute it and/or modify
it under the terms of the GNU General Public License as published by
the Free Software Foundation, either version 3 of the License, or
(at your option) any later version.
